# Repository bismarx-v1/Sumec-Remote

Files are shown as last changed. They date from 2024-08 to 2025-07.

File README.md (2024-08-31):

# IR Remote for SUMEC MiniSumo robot

## Description
Sumec-Remote repo contains files that are forked from p1rse as well as our own software, hardware and documentation for IR MiniSumo remote.

## Contents

- **-CODE-** Contains flashed code on the remote.
  
- **-DOCS-** Includes documentation about the project.

- **-PCB-** Includes schematics, bill of materials and pcb files. Schematic and PCBs are created using KiCAD.

## Contact
If you have any questions, suggestions, or issues regarding this project, please feel free to contact us: 

Email - savvapopov1804@gmail.com
LinkedIn - www.linkedin.com/in/popovsavvaprosek/

And follow us on the social media! 
Instagram - @sumec_minisumo_bot

**Sending love, from Czech Republic!**

## For information about the start module and its usage visit: http://www.startmodule.com

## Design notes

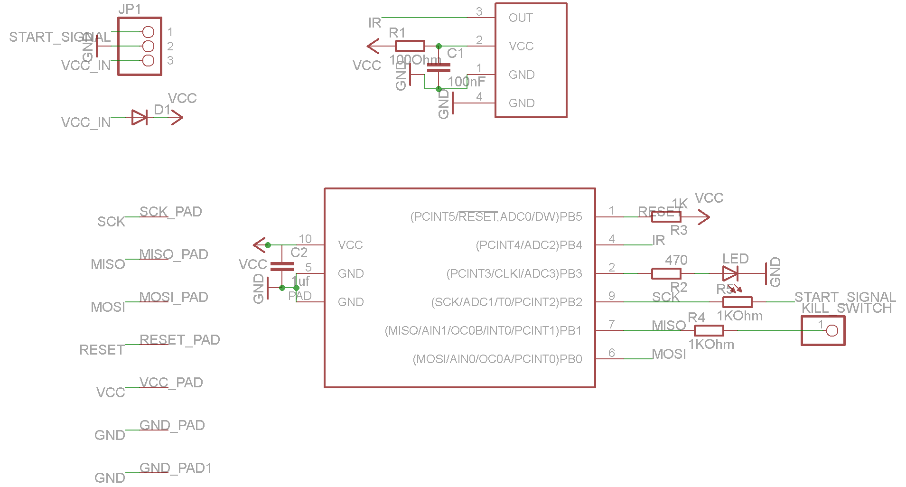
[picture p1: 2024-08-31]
_orig_main/Hardware/Prebuilt_Module/Version_0.16/Schematic_start_module_sumo_IR_V0_16.png

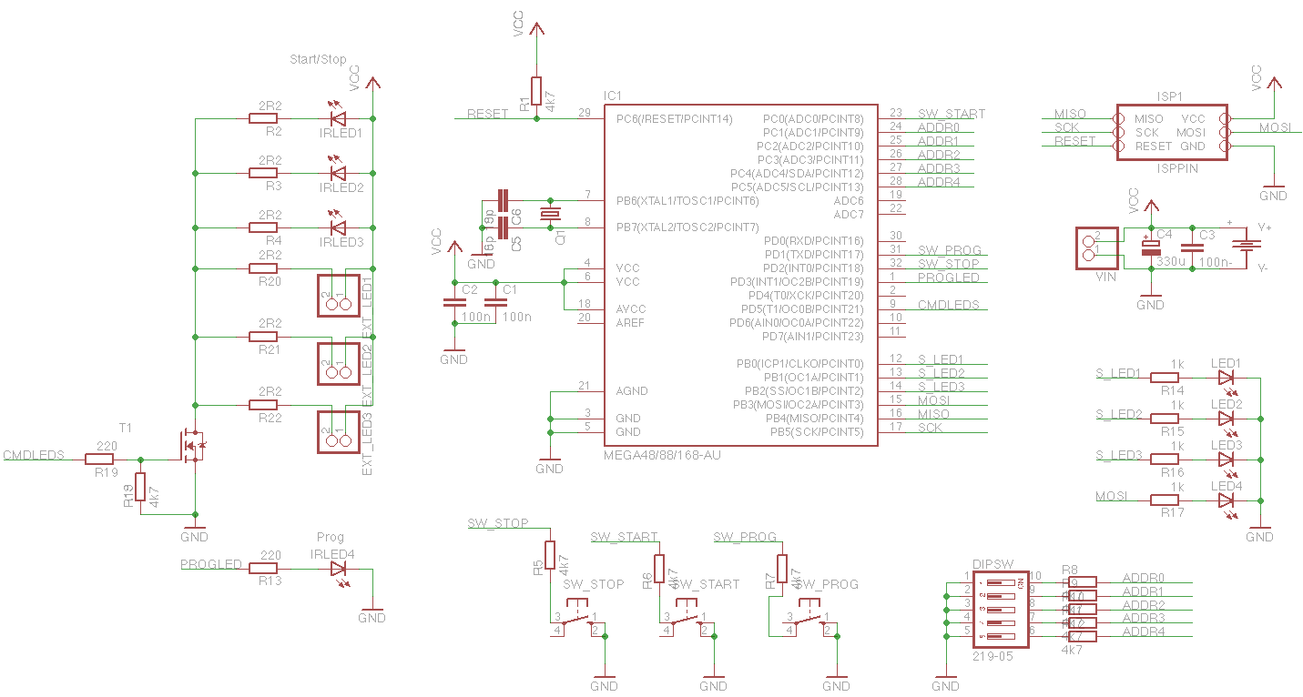
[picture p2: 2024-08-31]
_orig_main/Hardware/Remote_Control/Version_0.04/remote_schematic.png

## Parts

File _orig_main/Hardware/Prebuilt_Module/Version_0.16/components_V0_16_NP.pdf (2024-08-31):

Cost

Component | Package | value | Manufacturer | Mouser (part no) | 100.000 | 500.000 | 1000.000 | function
1 | ATTINY13A-MMU | MLF-10 | 556-ATTINY13A-MMU
IR | 1 | IR-receiver
LED | 1 | Green led | 0603 | 859-LTST-C190GKT | LED indications
C1,C2 | 2 | Capacitance | 0603 | 1uf | 810-C1608X7R1C105M
R1 | 1 | Resistance | 0603 | 100ohm | 667-ERJ-3GEYJ101V | to IR-receiver
R2 | 1 | Resistance | 0603 | 470ohm | 667-ERJ-3GEYJ471V
R3,R4,R5 | 3 | Resistance | 0603 | 1kohm | 667-ERJ-3GEYJ102V | pull up for signals out, pull up reset
D1 | 1 | Schottky Diode | SOD523 | 771-RB751S40,115
| | | | | 0.000 | 0.000 | 0.000
| | | | | 0.000 | 0.000 | 0.000

name in
schematic

amount per
board
uC | Atmel | Microcontroller
TSOP75338WTT 1 | Vishay
| | to Microcontroller and IR-receiver
| | resitor for LED
| | reverse polarity protection, as well as some noise cancelation
total (excl VAT)
total (inkl 20% VAT)

Note 1: Mouser doesn't keep this unit in stock, they do however keep TSOP75338WTR
the only difference is how they are packaged in the tape but for pick and place machines this can cause problems.

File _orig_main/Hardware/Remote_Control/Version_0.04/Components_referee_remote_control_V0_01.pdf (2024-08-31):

Sida

Name | Component | Quantity | Mouser article number | Total Price | Comments
B1 | Battery holder, 2xAA | 1 12BH212P-GR | 1.16 | 1.16
C1-C3 | 100nF | 3 581-08055C104J | 0.041 | 0.123
C4 | Capacitor, C6 (ø6.3mm), 330uF | 1 598-AVE337M06X16T-F | 0.083 | 0.083
C5-C6 | 18pF (optional) | 2 140-CC501N180J-RC | 0.053 | 0.106
Q1 | Crystal (optional), HC49S | 1 815-ABL-16-B2 | 0.27 | 0.27
DIPSW | 1 774-2195MST | 0.66 | 0.66
EXT_LED1-EXT_LED3 | 3 649-68000-420HLF | 0.041 | 0.123 20 pins total
IC1 | 1 556-ATMEGA168PA-AU | 2.1 | 2.1
IRLED1 - IRLED4 | 5mm IR LED | 4 78-TSUS5400 | 0.182 | 0.728
ISP | 1 649-67996-420HLF | 0.048 | 0.048 20 pins total
LED1-LED4 | 4 645-598-8170-107F | 0.1 | 0.4 Average price
T1 | MOSFET, N-channel, sot23, 6.5A | 1 621-DMG6968U-7 | 0.454 | 0.454
R1,R5-R12, R18 | 4k7 | 10 667-ERJ-6GEYJ472V | 0.033 | 0.33
R2-R4, R20-R22 | 2R2 | 6 667-ERJ-6GEYJ2R2V | 0.033 | 0.198
R13, R19 | 220 | 2 667-ERJ-6GEYJ221V | 0.033 | 0.066
R14-R17 | 1k | 4 667-ERJ-6GEYJ102V | 0.033 | 0.132
SW_PROG, SW_START, SW_STOP | Tactile switch, SKHHBV, pin, 6x6mm | 3 688-SKHHBV | 0.215 | 0.645
PCB | 1 N/A | 3 | 3 @10pcs
10.626 <-Total

Price (1pcs, €, excl. vat)

Dipswitch, 5 pol
Pinheader, 1x2
Atmega48/88/168-AU

Pinheader, 2x3
Indication LED, 0805, any colour, Vf<3V SOT223 – 771-BUK9880-55135

By sternå

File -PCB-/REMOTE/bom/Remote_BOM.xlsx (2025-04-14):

Value | Link | Reserve | Quantity | Footprint
10uF | 10uF, 16V, 1206, tantal, mouser (https://cz.mouser.com/ProductDetail/KEMET/T491A106K016AT) | >30 | 2 | CP_EIA-3216-18_Kemet-A_Pad1.58x1.35mm_HandSolder
100nF | 100nF, 16V, 0805, ceramic, mouser X7R (https://cz.mouser.com/ProductDetail/YAGEO/AC0805KRX7R7BB104) | >80 | 2 | C_0805_2012Metric_Pad1.18x1.45mm_HandSolder
18pF | 18pF, 16V, 0805, ceramic, mouser (https://cz.mouser.com/ProductDetail/KYOCERA-AVX/0805YA180JAT2A?qs=nl0EtZFOfLiGc7H%252BYUnNHw%3D%3D) |  | 2 | C_0805_2012Metric_Pad1.18x1.45mm_HandSolder
10k | 10k, 250mW, 0805, mouser (https://cz.mouser.com/ProductDetail/Vishay-Dale/RCC080510K0FKEA?qs=GedFDFLaBXGY93oge9hajw%3D%3D) |  | 5 | R_0805_2012Metric_Pad1.20x1.40mm_HandSolder
1k | 1k. 500mW, 0805, mouser (https://cz.mouser.com/ProductDetail/Vishay-Dale/CRCW08051K00FKEAHP?qs=FlFvgi4rxBy%252Bn2DMV%2FkIbA%3D%3D) |  | 4 | R_0805_2012Metric_Pad1.20x1.40mm_HandSolder
200R | 200R, 500mW, 0805, mouser (https://cz.mouser.com/ProductDetail/Vishay-Dale/CRCW0805200RFKEAHP?qs=2Xec%252BEQj5n%252BcRsKDNXpbZw%3D%3D) |  | 2 | R_0805_2012Metric_Pad1.20x1.40mm_HandSolder
2.2R | 2.2R, 500mW, 0805, mouser (https://cz.mouser.com/ProductDetail/Vishay-Dale/CRCW08052R20FKEAHP?qs=40TFAHZMFvc8altFjF5kRw%3D%3D) |  | 3 | R_0805_2012Metric_Pad1.20x1.40mm_HandSolder
YC248-JR-0710KL | 10k, 8x0402, mouser (https://cz.mouser.com/ProductDetail/YAGEO/YC248-JR-0710KL?qs=8cPjvKtxWv7XgZyJevtvWg%3D%3D) |  | 1 | resistor_array
LED | Yellow, Red, Green (NIO) | 8,8,18 | 4 | LED_0805_2012Metric_Pad1.15x1.40mm_HandSolder
IR204A | IR LED, 50mA, 1.3V, mouser (https://cz.mouser.com/ProductDetail/ROHM-Semiconductor/SIR-34ST3F?qs=4kLU8WoGk0sGjEX1Vu2vfA%3D%3D) |  | 4 | LED_D3.0mm_Horizontal_O3.81mm_Z10.0mm | Red LED, 20mA 1.9V, 0805, mouser (https://cz.mouser.com/ProductDetail/Stanley-Electric/VFHV1112H-3BZ2B-TR?qs=byeeYqUIh0PKiA%252BYRcKo5Q%3D%3D)
Crystal - ABM8G | 16 MHz, 18 pF, mouser (https://www.mouser.co.uk/ProductDetail/ABRACON/ABM8G-16.000MHZ-18-D2Y-T?qs=3LVMET7lfiPkoUdIbdKAPg%3D%3D) |  | 1 | crystal_smd | Yellow LED, 20mA, 1.9V, 0805, mouser (https://cz.mouser.com/ProductDetail/Stanley-Electric/FY1112H-TR?qs=byeeYqUIh0M%2F1I90%252BhjkXg%3D%3D)
DMG6968U-7 | NMOS, SOT23-3, mouser (https://eu.mouser.com/ProductDetail/Diodes-Incorporated/DMG6968U-7?qs=oUsD4qhOtFxfxyoeWY4RMA%3D%3D) |  | 1 | TSOT-23-3_HandSoldering | Green-Yellow LED, 20mA, 1.9V, mouser (https://cz.mouser.com/ProductDetail/Stanley-Electric/VFHD1112H-3B72B-TR?qs=byeeYqUIh0N1xLw8fV03PA%3D%3D)
ATmega168PA-AU | TQFP-32, 1.8 - 5.5 [V], mouser (https://cz.mouser.com/ProductDetail/Microchip-Technology/ATMEGA168PA-AU?qs=rBGENRD8NwK93x8%252BpfprPQ%3D%3D) |  | 1 | TQFP-32_7x7mm_P0.8mm
SW_Push | Height 8mm, Width 6mm, mouser (https://cz.mouser.com/ProductDetail/TE-Connectivity-AMP/FSM11JLH?qs=P19jvy6W2mdQ1kTiQwvziQ%3D%3D) |  | 3 | SW_PUSH_6mm
DS04-254-1-05BK-SMT | 5P, 2.54mm, DIP, mouser (https://cz.mouser.com/ProductDetail/CUI-Devices/DS04-254-1-05BK-SMT?qs=wnTfsH77Xs5Ndj%252Bt08dChA%3D%3D) |  | 1 | dip_switch
Battery | Keystone_2462, 2xAA, mouser (https://cz.mouser.com/ProductDetail/Keystone-Electronics/2462?qs=3CbvriavsLChvFNADwDLZA%3D%3D) |  | 1 | BatteryHolder_Keystone_2462_2xAA - no holes
AVR-ISP-6 | GME |  | 1 | PinHeader_2x03_P2.54mm_Vertical
NIO - Not in order

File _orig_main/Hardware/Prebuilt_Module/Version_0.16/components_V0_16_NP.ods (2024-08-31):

 |  |  |  |  |  |  |  | Cost
name in schematic | amount per board | Component | Package | value | Manufacturer | Mouser (part no) | 100.000 | 500.000 | 1000.000 | function
uC | 1 | ATTINY13A-MMU | MLF-10 |  | Atmel | 556-ATTINY13A-MMU |  |  |  | Microcontroller
IR | 1 | TSOP75338WTT 1 |  |  | Vishay |  |  |  |  | IR-receiver
LED | 1 | Green led | 0603 |  |  | 859-LTST-C190GKT |  |  |  | LED indications
C1,C2 | 2 | Capacitance | 0603 | 1uf |  | 810-C1608X7R1C105M |  |  |  | to Microcontroller and IR-receiver
R1 | 1 | Resistance | 0603 | 100ohm |  | 667-ERJ-3GEYJ101V |  |  |  | to IR-receiver
R2 | 1 | Resistance | 0603 | 470ohm |  | 667-ERJ-3GEYJ471V |  |  |  | resitor for LED
R3,R4,R5 | 3 | Resistance | 0603 | 1kohm |  | 667-ERJ-3GEYJ102V |  |  |  | pull up for signals out, pull up reset
D1 | 1 | Schottky Diode | SOD523 |  |  | 771-RB751S40,115 |  |  |  | reverse polarity protection, as well as some noise cancelation
 |  | total (excl VAT) |  |  |  |  | 0.000 | 0.000 | 0.000
 |  | total (inkl 20% VAT) |  |  |  |  | 0.000 | 0.000 | 0.000
 |  | Note 1: Mouser doesn't keep this unit in stock, they do however keep TSOP75338WTR the only difference is how they are packaged in the tape but for pick and place machines this can cause problems.

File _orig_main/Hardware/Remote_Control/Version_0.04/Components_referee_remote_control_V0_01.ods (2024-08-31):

Name | Component | Quantity | Mouser article number | Price (1pcs, €, excl. vat) | Total Price | Comments
B1 | Battery holder, 2xAA | 1 | 12BH212P-GR | 1.16 | 1.16
C1-C3 | 100nF | 3 | 581-08055C104J | 0.041 | 0.123
C4 | Capacitor, C6 (ø6.3mm), 330uF | 1 | 598-AVE337M06X16T-F | 0.083 | 0.083
C5-C6 | 18pF (optional) | 2 | 140-CC501N180J-RC | 0.053 | 0.106
Q1 | Crystal (optional), HC49S | 1 | 815-ABL-16-B2 | 0.27 | 0.27
DIPSW | Dipswitch, 5 pol | 1 | 774-2195MST | 0.66 | 0.66
EXT_LED1-EXT_LED3 | Pinheader, 1x2 | 3 | 649-68000-420HLF | 0.041 | 0.123 | 20 pins total
IC1 | Atmega48/88/168-AU | 1 | 556-ATMEGA168PA-AU | 2.1 | 2.1
IRLED1 - IRLED4 | 5mm IR LED | 4 | 78-TSUS5400 | 0.182 | 0.728
ISP | Pinheader, 2x3 | 1 | 649-67996-420HLF | 0.048 | 0.048 | 20 pins total
LED1-LED4 | Indication LED, 0805, any colour, Vf<3V | 4 | 645-598-8170-107F | 0.1 | 0.4 | Average price
T1 | MOSFET, N-channel, sot23, 6.5A | 1 | 621-DMG6968U-7 | 0.454 | 0.454 | SOT223 – 771-BUK9880-55135
R1,R5-R12, R18 | 4k7 | 10 | 667-ERJ-6GEYJ472V | 0.033 | 0.33
R2-R4, R20-R22 | 2R2 | 6 | 667-ERJ-6GEYJ2R2V | 0.033 | 0.198
R13, R19 | 220 | 2 | 667-ERJ-6GEYJ221V | 0.033 | 0.066
R14-R17 | 1k | 4 | 667-ERJ-6GEYJ102V | 0.033 | 0.132
SW_PROG, SW_START, SW_STOP | Tactile switch, SKHHBV, pin, 6x6mm | 3 | 688-SKHHBV | 0.215 | 0.645
PCB | By sternå | 1 | N/A | 3 | 3 | @10pcs
 |  |  |  |  | 10.626 | <-Total

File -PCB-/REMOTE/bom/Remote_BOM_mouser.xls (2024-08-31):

Mfr Part Number (Input) | Manufacturer Part Number | Mouser Part Number | Manufacturer Name | Description | Quantity 1 | Unit Price 1 | Quantity 2 | Unit Price 2 | Quantity 3 | Unit Price 3 | Quantity 4 | Unit Price 4 | Quantity 5 | Unit Price 5 | Order Quantity | Order Unit Price | Min./Mult. | Availability | Lead Time in Days | Lifecycle | NCNR | RoHS | Pb Free | Package Type | Datasheet URL | Product Image | Design Risk
 |  | 581-0805YA180JAT2A |  |  | 10
 |  | 71-RCC080510K0FKEA |  |  | 100
 |  | 71-CRCW08051K00FKEAH |  |  | 10
 |  | 71-CRCW0805200RFKEAH |  |  | 10
 |  | 71-CRCW08052R20FKEAH |  |  | 10
 |  | 603-YC248-JR-0710KL |  |  | 10
 |  | 755-SIR-34ST3F |  |  | 10
 |  | 815-ABM8G-16-18D2Y |  |  | 10
 |  | 621-DMG6968U-7 |  |  | 10
 |  | 556-ATMEGA168PA-AU |  |  | 3
 |  | 506-FSM11JLH |  |  | 10
 |  | 490-DS04254105BK-SMT |  |  | 3
 |  | 534-2462 |  |  | 3

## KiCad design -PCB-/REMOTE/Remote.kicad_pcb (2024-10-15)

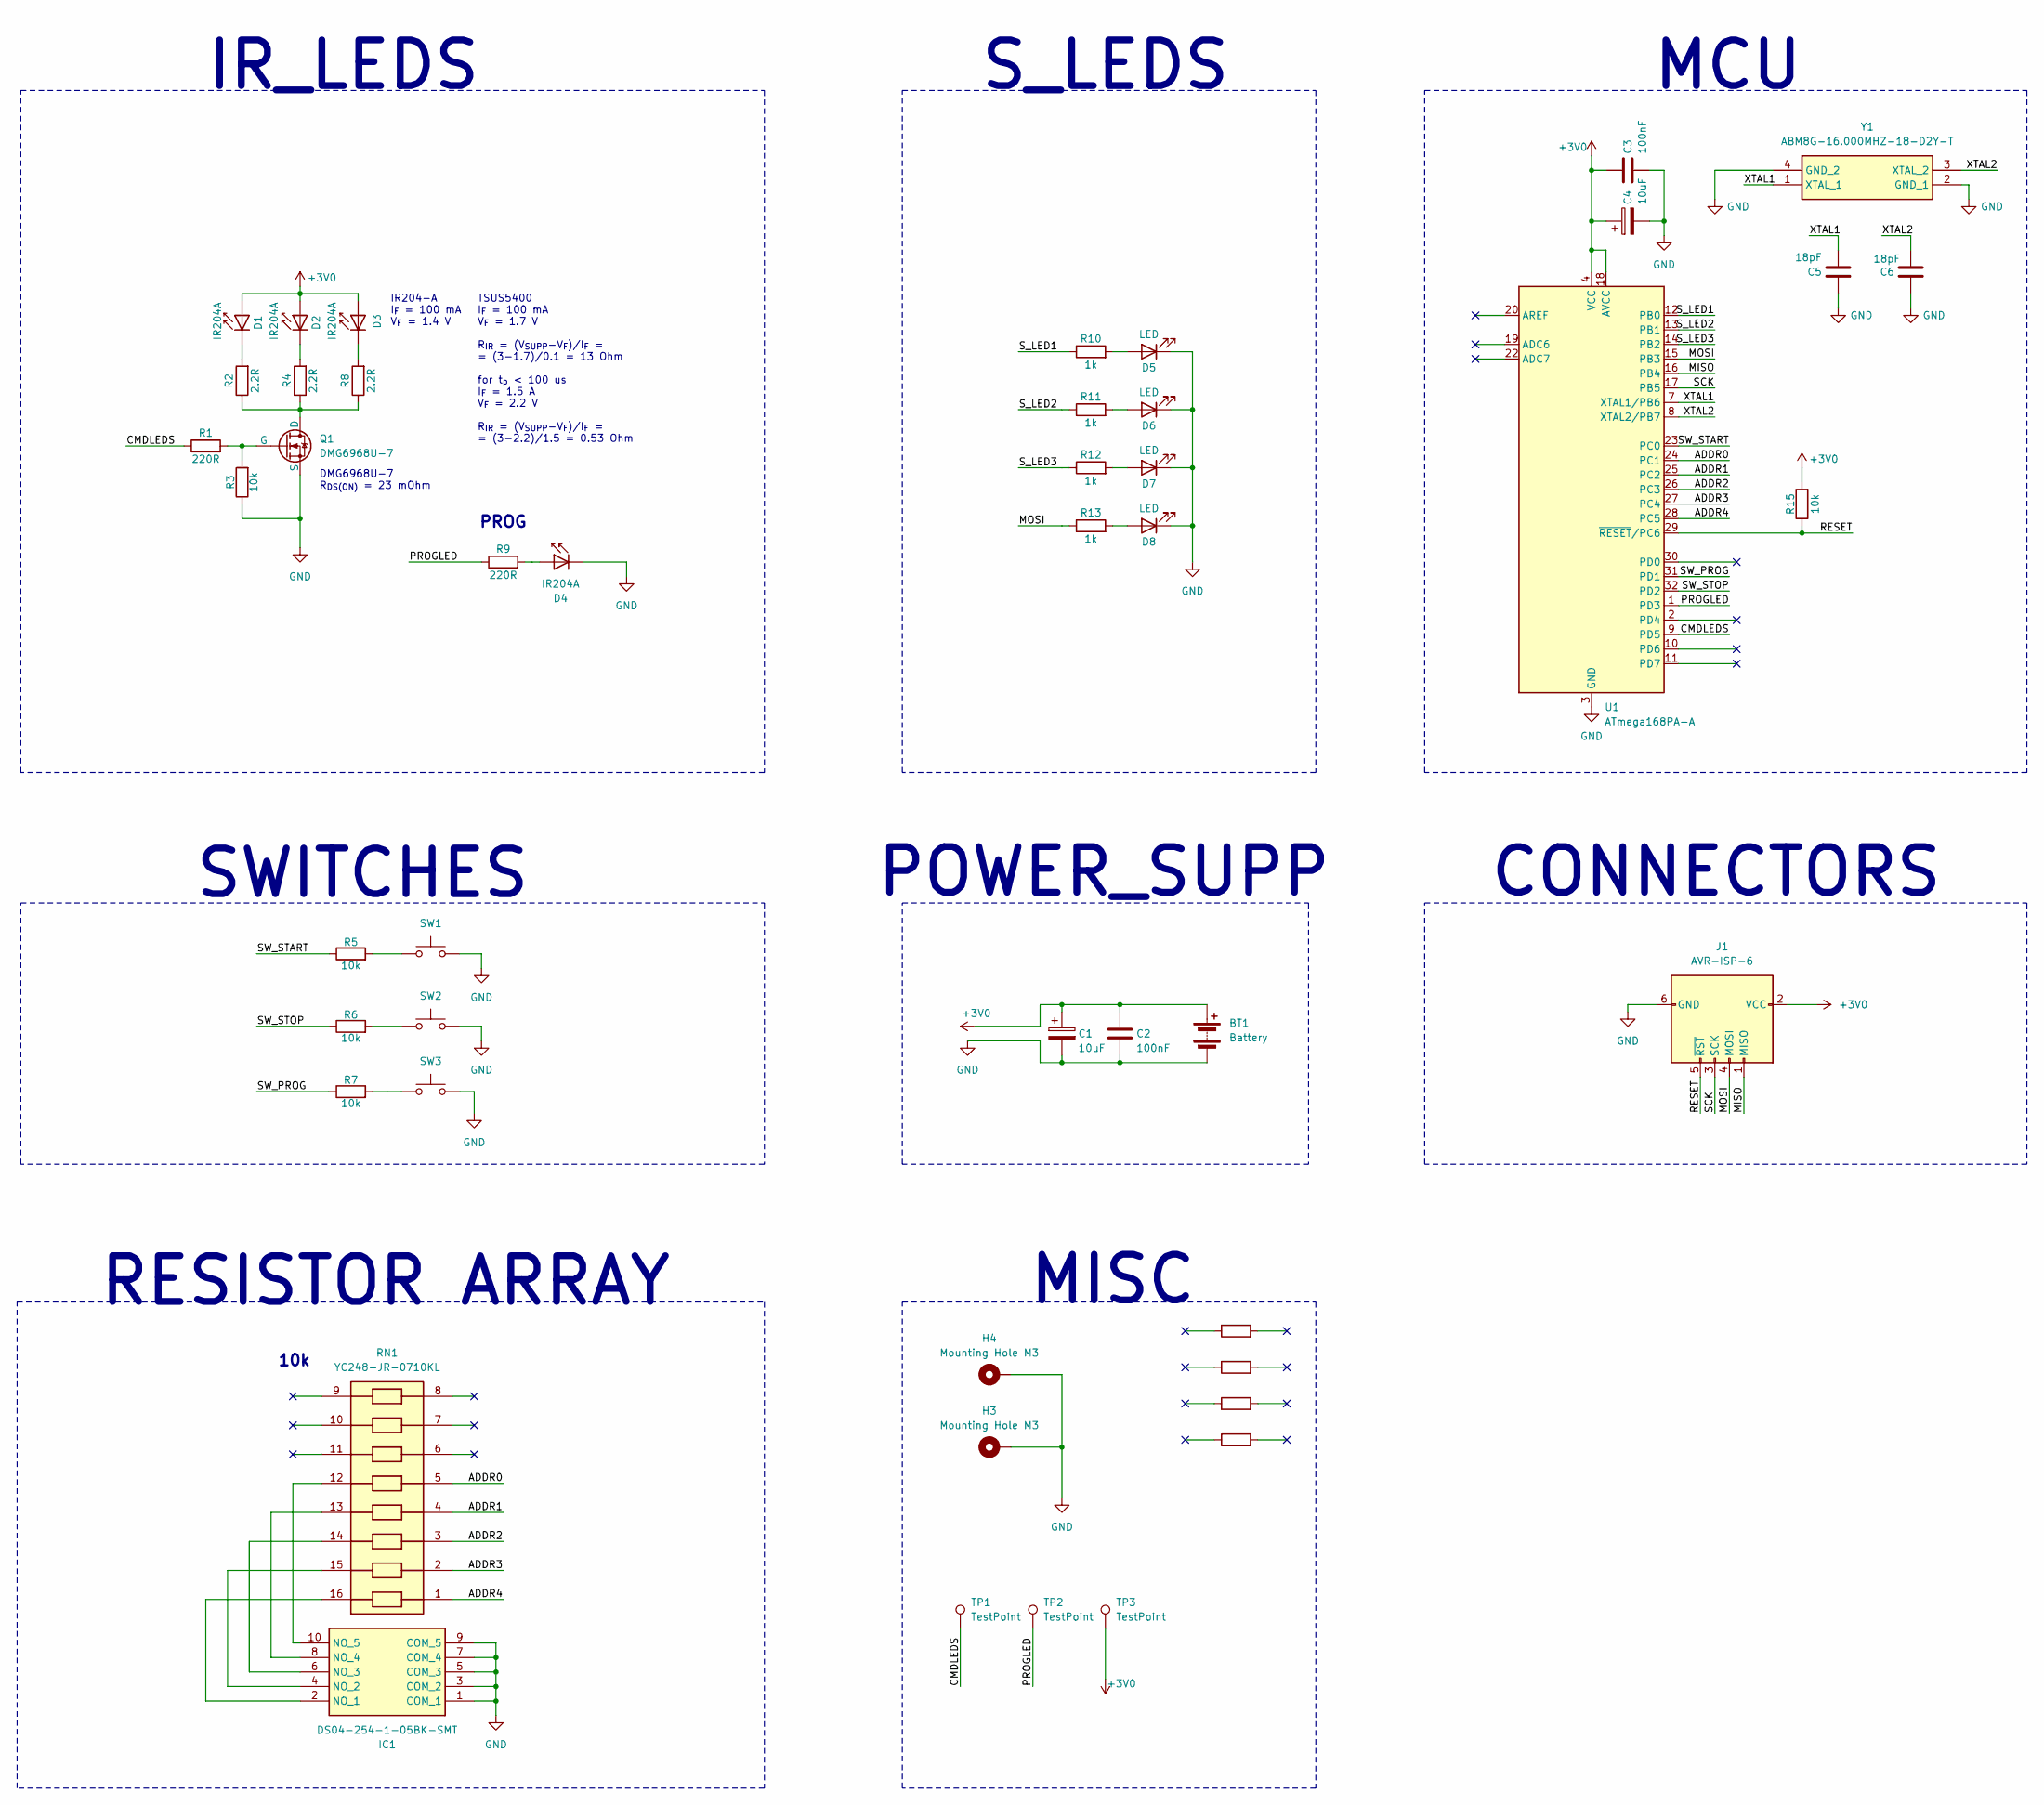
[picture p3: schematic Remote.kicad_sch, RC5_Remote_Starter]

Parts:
BT1: Battery; BatteryHolder_Keystone_2462_2xAA - no holes
C1, C4: 10uF; CP_EIA-3216-18_Kemet-A_Pad1.58x1.35mm_HandSolder
C2, C3: 100nF; C_0805_2012Metric_Pad1.18x1.45mm_HandSolder
C5, C6: 18pF; C_0805_2012Metric_Pad1.18x1.45mm_HandSolder
D1, D3: IR204A; LED_D3.0mm_Horizontal_O3.81mm_Z10.0mm_no_silk
D2: IR204A; LED_D3.0mm_Horizontal_O3.81mm_Z10.0mm_flipped_no_silk
D4: IR204A; LED_D3.0mm_Horizontal_O3.81mm_Z10.0mm_flipped
D5, D6, D7, D8: LED; LED_0805_2012Metric_Pad1.15x1.40mm_HandSolder
H3, H4: Mounting Hole M3; MountingHole_3.2mm_M3_Pad_Via
IC1: DS04-254-1-05BK-SMT; dip_switch; Mouser Part Number 490-DS04254105BK-SMT
J1: AVR-ISP-6; PinHeader_2x03_P2.54mm_Vertical
Q1: DMG6968U-7; SOT-23-3
R1, R9: 220R; R_0805_2012Metric_Pad1.20x1.40mm_HandSolder
R2, R4, R8: 2.2R; R_0805_2012Metric_Pad1.20x1.40mm_HandSolder
R3, R5, R6, R7, R15: 10k; R_0805_2012Metric_Pad1.20x1.40mm_HandSolder
R10, R11, R12, R13: 1k; R_0805_2012Metric_Pad1.20x1.40mm_HandSolder
R14: R; purosidenegative
R16: R; SPS LOGO
R17: R; boi
R18: R; Logo
RN1: YC248-JR-0710KL; resistor_array; Mouser Part Number 603-YC248-JR-0710KL
SW1, SW2, SW3: SW_Push; SW_PUSH_6mm
TP1, TP2, TP3: TestPoint; TestPoint_Pad_D1.5mm
U1: ATmega168PA-A; TQFP-32_7x7mm_P0.8mm
Y1: ABM8G-16.000MHZ-18-D2Y-T; crystal_smd; Mouser Part Number 815-ABM8G-16-18D2Y

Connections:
+3V0: BT1.1 (+), C1.1, C2.1, C3.1, C4.1, D1.2 (A), D2.2 (A), D3.2 (A), J1.2 (VCC), R15.2, TP3.1, U1.4 (VCC), U1.6 (VCC), U1.18 (AVCC)
/ADDR0: RN1.5, U1.24 (PC1)
/ADDR1: RN1.4, U1.25 (PC2)
/ADDR2: RN1.3, U1.26 (PC3)
/ADDR3: RN1.2, U1.27 (PC4)
/ADDR4: RN1.1, U1.28 (PC5)
/CMDLEDS: R1.1, TP1.1, U1.9 (PD5)
/MISO: J1.1 (MISO), U1.16 (PB4)
/MOSI: J1.4 (MOSI), R13.1, U1.15 (PB3)
/PROGLED: R9.1, TP2.1, U1.1 (PD3)
/RESET: J1.5 (~RST), R15.1, U1.29 (~RESET/PC6)
/SCK: J1.3 (SCK), U1.17 (PB5)
/SW_PROG: R7.1, U1.31 (PD1)
/SW_START: R5.1, U1.23 (PC0)
/SW_STOP: R6.1, U1.32 (PD2)
/S_LED1: R10.1, U1.12 (PB0)
/S_LED2: R11.1, U1.13 (PB1)
/S_LED3: R12.1, U1.14 (PB2)
/XTAL1: C5.2, U1.7 (XTAL1/PB6), Y1.1 (XTAL_1)
/XTAL2: C6.2, U1.8 (XTAL2/PB7), Y1.3 (XTAL_2)
GND: BT1.2 (-), C1.2, C2.2, C3.2, C4.2, C5.1, C6.1, D4.1 (K), D5.1 (K), D6.1 (K), D7.1 (K), D8.1 (K), H3.1, H4.1, IC1.1 (COM_1), IC1.3 (COM_2), IC1.5 (COM_3), IC1.7 (COM_4), IC1.9 (COM_5), J1.6 (GND), Q1.3 (S), R3.1, SW1.2, SW2.2, SW3.2, U1.3 (GND), U1.5 (GND), U1.21 (GND), Y1.2 (GND_1), Y1.4 (GND_2)
unnamed: D1.1 (K), R2.2
unnamed: D2.1 (K), R4.2
unnamed: D3.1 (K), R8.2
unnamed: D4.2 (A), R9.2
unnamed: D5.2 (A), R10.2
unnamed: D6.2 (A), R11.2
unnamed: D7.2 (A), R12.2
unnamed: D8.2 (A), R13.2
unnamed: IC1.2 (NO_1), RN1.16
unnamed: IC1.4 (NO_2), RN1.15
unnamed: IC1.6 (NO_3), RN1.14
unnamed: IC1.8 (NO_4), RN1.13
unnamed: IC1.10 (NO_5), RN1.12
unnamed: Q1.1 (D), R2.1, R4.1, R8.1
unnamed: Q1.2 (G), R1.2, R3.2
unnamed: R5.2, SW1.1
unnamed: R6.2, SW2.1
unnamed: R7.2, SW3.1

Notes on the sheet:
MISC
MCU
IR204-A I_{F} = 100 mA V_{F} = 1.4 V
SWITCHES
10k
POWER_SUPP
RESISTOR ARRAY
TSUS5400 I_{F} = 100 mA V_{F} = 1.7 V R_{IR} = (V_{SUPP}-V_{F})/I_{F} = = (3-1.7)/0.1 = 13 Ohm for t_{p} < 100 us I_{F} = 1.5 A V_{F} = 2.2 V R_{IR} = (V_{SUPP}-V_{F})/I_{F} = = (3-2.2)/1.5 = 0.53 Ohm
S_LEDS
CONNECTORS
IR_LEDS
PROG
DMG6968U-7 R_{DS(ON)} = 23 mOhm

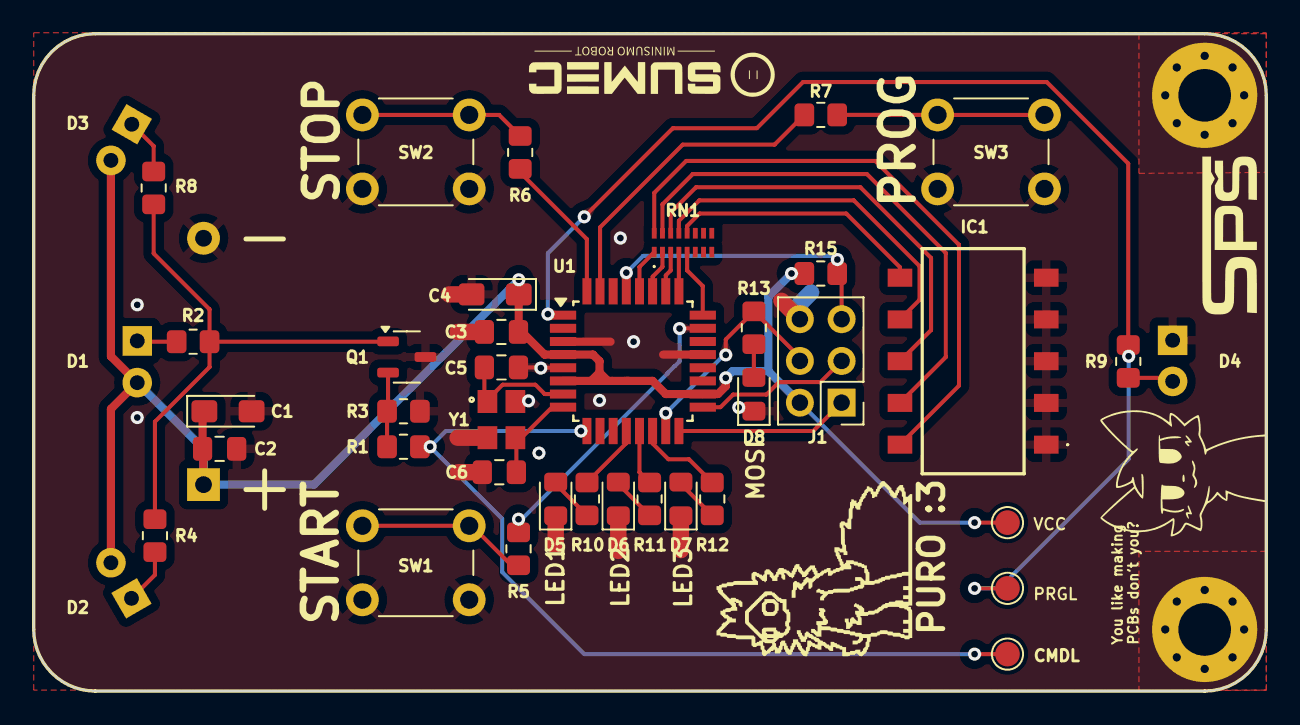
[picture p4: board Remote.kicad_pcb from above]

Board: 2 copper layers, 75.0 x 40.0 mm, 47 parts (1 on the bottom side), 39 nets.

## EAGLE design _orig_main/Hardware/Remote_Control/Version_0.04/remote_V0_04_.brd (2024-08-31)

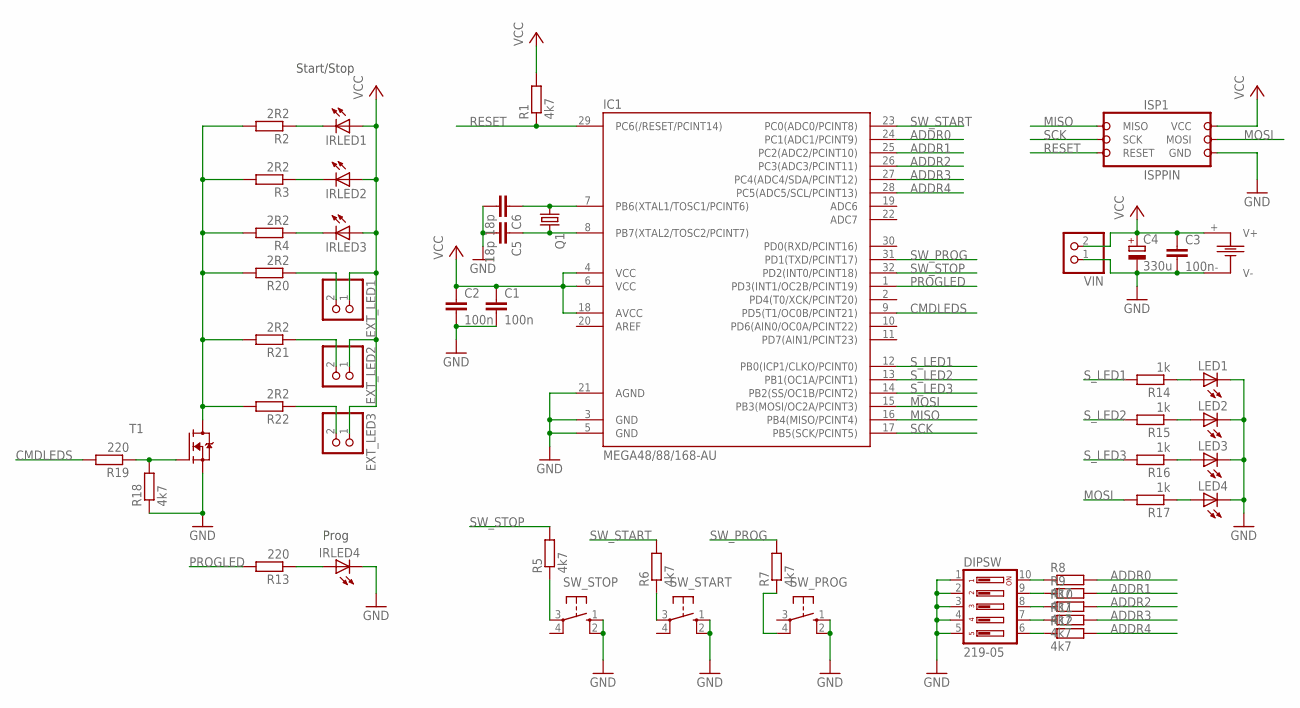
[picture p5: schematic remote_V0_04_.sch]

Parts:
B1: BATTERY_HOLDER_1; BAT_HOLDER_1
C1, C2, C3: 100n; C0805WP
C4: 330u; SANYO-OSCON_SMD_C6
C5, C6: 18p; C0805WP
DIPSW: 219-05; CTS-219-05
EXT_LED1, EXT_LED2, EXT_LED3: PINHD-1X2LONG; 1X2LONG
IC1: MEGA48/88/168-AU; TQFP32-08
IRLED1, IRLED2, IRLED3, IRLED4: LEDLED5MMH; LED5MMH
ISP1: ISPPIN; 2X03
LED1, LED2, LED3, LED4: LED0805; LED_0805
Q1: CRYSTALHC49S; HC49/S
R1, R5, R6, R7, R8, R9, R10, R11, R12, R18: 4k7; R0805WP
R2, R3, R4, R20, R21, R22: 2R2; R0805WP
R13, R19: 220; R0805WP
R14, R15, R16, R17: 1k; R0805WP
SW_PROG: 10-XX; B3F-10XX
SW_START: 10-XX; B3F-10XX
SW_STOP: 10-XX; B3F-10XX
T1: MOSFET_N_SOT23; SOT23
VIN: PINHD-1X2; 1X02

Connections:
ADDR0: IC1.24 (PC1(ADC1/PCINT9)), R8.2
ADDR1: IC1.25 (PC2(ADC2/PCINT10)), R9.2
ADDR2: IC1.26 (PC3(ADC3/PCINT11)), R10.2
ADDR3: IC1.27 (PC4(ADC4/SDA/PCINT12)), R11.2
ADDR4: IC1.28 (PC5(ADC5/SCL/PCINT13)), R12.2
CMDLEDS: IC1.9 (PD5(T1/OC0B/PCINT21)), R19.2
GND: B1.- (V-), C1.2, C2.2, C3.2, C4.-, C5.2, C6.2, DIPSW.1, DIPSW.2, DIPSW.3, DIPSW.4, DIPSW.5, IC1.3 (GND), IC1.5 (GND), IC1.21 (AGND), IRLED4.P$2 (C), ISP1.6 (GND), LED1.C, LED2.C, LED3.C, LED4.C, R18.1, SW_PROG.1 (S), SW_PROG.2 (S1), SW_START.1 (S), SW_START.2 (S1), SW_STOP.1 (S), SW_STOP.2 (S1), T1.2 (S), VIN.1
MISO: IC1.16 (PB4(MISO/PCINT4)), ISP1.1 (MISO)
MOSI: IC1.15 (PB3(MOSI/OC2A/PCINT3)), ISP1.4 (MOSI), R17.2
unnamed: IRLED1.P$2 (C), R2.1
unnamed: IRLED2.P$2 (C), R3.1
unnamed: IRLED3.P$2 (C), R4.1
unnamed: DIPSW.10, R8.1
unnamed: DIPSW.9, R9.1
unnamed: DIPSW.8, R10.1
unnamed: DIPSW.7, R11.1
unnamed: DIPSW.6, R12.1
unnamed: R5.1, SW_STOP.3
unnamed: R6.1, SW_START.3
unnamed: R7.1, SW_PROG.4 (P1)
unnamed: IRLED4.P$1 (A), R13.1
unnamed: R18.2, R19.1, T1.1 (G)
unnamed: LED1.A, R14.1
unnamed: LED2.A, R15.1
unnamed: LED3.A, R16.1
unnamed: LED4.A, R17.1
unnamed: C6.1, IC1.7 (PB6(XTAL1/TOSC1/PCINT6)), Q1.1
unnamed: EXT_LED1.2, R20.1
unnamed: EXT_LED2.2, R21.1
unnamed: R2.2, R3.2, R4.2, R20.2, R21.2, R22.2, T1.3 (D)
unnamed: EXT_LED3.2, R22.1
unnamed: C5.1, IC1.8 (PB7(XTAL2/TOSC2/PCINT7)), Q1.2
PROGLED: IC1.1 (PD3(INT1/OC2B/PCINT19)), R13.2
RESET: IC1.29 (PC6(/RESET/PCINT14)), ISP1.5 (RESET), R1.1
SCK: IC1.17 (PB5(SCK/PCINT5)), ISP1.3 (SCK)
SW_PROG: IC1.31 (PD1(TXD/PCINT17)), R7.2
SW_START: IC1.23 (PC0(ADC0/PCINT8)), R6.2
SW_STOP: IC1.32 (PD2(INT0/PCINT18)), R5.2
S_LED1: IC1.12 (PB0(ICP1/CLKO/PCINT0)), R14.2
S_LED2: IC1.13 (PB1(OC1A/PCINT1)), R15.2
S_LED3: IC1.14 (PB2(SS/OC1B/PCINT2)), R16.2
VCC: B1.+ (V+), C1.1, C2.1, C3.1, C4.+, EXT_LED1.1, EXT_LED2.1, EXT_LED3.1, IC1.4 (VCC), IC1.6 (VCC), IC1.18 (AVCC), IRLED1.P$1 (A), IRLED2.P$1 (A), IRLED3.P$1 (A), ISP1.2 (VCC), R1.2, VIN.2

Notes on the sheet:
Start/Stop
Prog

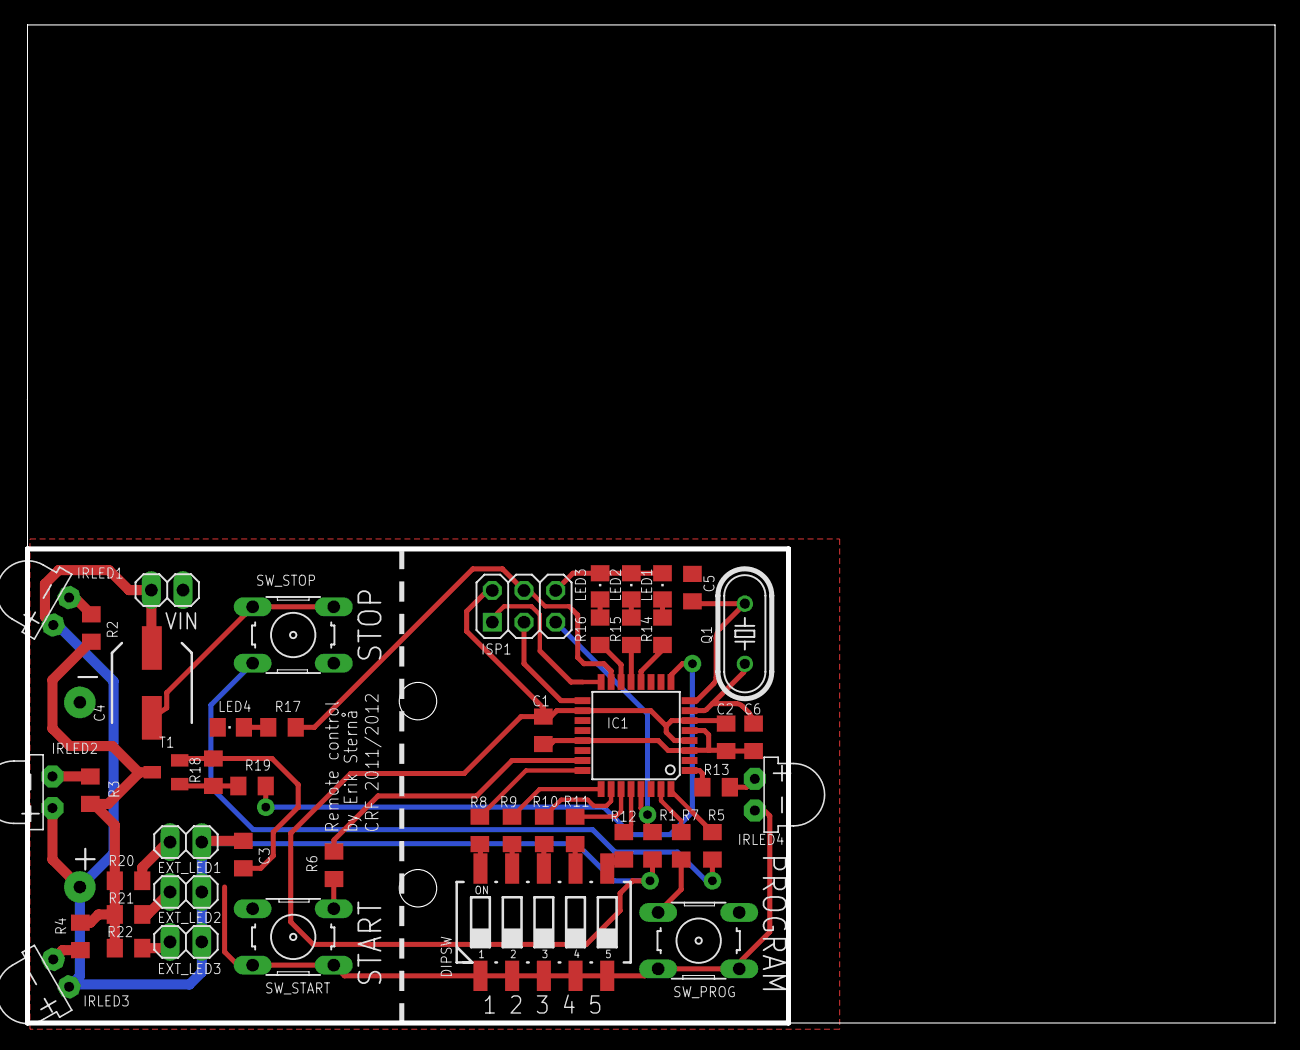
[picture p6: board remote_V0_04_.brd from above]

Board: 2 copper layers, 100.0 x 80.0 mm, 49 parts (1 on the bottom side), 42 nets.

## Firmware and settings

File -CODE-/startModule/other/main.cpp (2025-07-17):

#if 0
/**
 * https://www.instructables.com/ATTiny-Port-Manipulation/
 * https://www.instructables.com/ATtiny85-Interrupt-Barebones-Example/
 * https://en.wikipedia.org/wiki/RC-5
 */

/**
 * This feels like a lot of janky hacked together trash.
 * Hope it works.
 */

  #include <Arduino.h>


  #define PIN_STATE_OUT 3
  #define PIN_IR_INPUT  4
  #define PIN_LED1      1
  #define PIN_LED2      0

  #define RECIEVE_TIMEOUT 3    // In ms. How long since the last trigger should be considered an end.
  #define BIT_MIN_TIME    750  // In us. Anything shorter than this is noise.
  #define BUFFER_SIZE     32


  #define PROTOCOL_RC5    1
  #define RC5_SINGLE_LOW  800
  #define RC5_SINGLE_HIGH 1000
  #define RC5_DOUBLE_LOW  1600
  #define RC5_DOUBLE_HIGH 2000


  #define SET_TO_BIT(BIT, OUT_ARRAY_INDEX, OUT_ARRAY)                                                                          \
    if((BIT) == 0) {                                                                                                           \
      OUT_ARRAY &= 1 << OUT_ARRAY_INDEX;                                                                                       \
    } else {                                                                                                                   \
      OUT_ARRAY |= 0 << OUT_ARRAY_INDEX;                                                                                       \
    }

  #define DIV_TWO_CEIL(SRC, DST)                                                                                               \
    if((SRC & 1) == 1) {                                                                                                       \
      DST = SRC >> 1;                                                                                                          \
      DST = SRC + 1;                                                                                                           \
    } else {                                                                                                                   \
      DST = SRC >> 1;                                                                                                          \
    }



uint64_t             rawBuffer                    = 0;
static const uint8_t rawBufferSize                = (BUFFER_SIZE < sizeof(rawBuffer) * 8 ? BUFFER_SIZE : sizeof(rawBuffer) * 8);
uint16_t             rawBufferTime[rawBufferSize] = {0};
uint8_t              rawBufferIndex               = 0;
uint32_t             recieveTimeoutTime           = -1;



void irInterrupt() {
  static uint32_t timeSinceLastTrig = 0;

  // Read the volatile stuff.
  uint32_t timeNow = micros();
  bool     irVal   = (DDRB >> PIN_IR_INPUT) & PB1;


  // Write the length of the previous bit.
  rawBufferTime[rawBufferIndex] = timeNow - timeSinceLastTrig;

  // Move to the current bit.
  rawBufferIndex++;
  // If buffer full, return.
  if(rawBufferIndex + 1 >= rawBufferSize) {
    return;
  }

  // Add the value to the buffer.
  SET_TO_BIT(irVal, rawBufferIndex, rawBuffer)
  // Update time since last trig.
  timeSinceLastTrig = timeNow;

  // Update the timeout time.
  recieveTimeoutTime = millis() + RECIEVE_TIMEOUT;
}


uint64_t             cleanBuffer     = 0;
static const uint8_t cleanBufferSize = (BUFFER_SIZE < sizeof(cleanBuffer) * 8 ? BUFFER_SIZE : sizeof(cleanBuffer) * 8);
uint16_t             cleanBufferTime[cleanBufferSize] = {0};
uint8_t              cleanBufferIndex                 = 0;

void reduceBuffer() {
  static uint8_t bitWriteIdx = 0;
  for(uint8_t idx = 0; idx < cleanBufferIndex; idx++) {
    static uint8_t bitPrevoius = 0xff;
    bool           bitCurrent  = (cleanBuffer >> idx) & 1;
    if(bitPrevoius == bitCurrent) {
      // Add this bit's length to the prevoius one.
      cleanBufferTime[bitWriteIdx - 1] += cleanBufferTime[idx];
    } else {
      // Just move the bit to a new pos.
      SET_TO_BIT(bitCurrent, cleanBuffer, bitWriteIdx)
      cleanBufferTime[bitWriteIdx] = cleanBufferTime[idx];
      bitWriteIdx++;
    }

    bitPrevoius = bitCurrent;
  }
}


void denoiseBuffer() {
  uint16_t accumulatedTime = 0;
  // Check the length of every bit.
  for(uint8_t idx = 0; idx < rawBufferIndex; idx++) {
    accumulatedTime += rawBufferTime[idx];
    // Isn't noise.
    if(rawBufferTime[idx] >= BIT_MIN_TIME) {
      // Shift the bit into the clean buffer.
      SET_TO_BIT((rawBuffer >> idx) & 1, cleanBufferIndex, cleanBuffer)
      // Set the bits length since the prevoius "clean" bit.
      cleanBufferTime[cleanBufferIndex] = accumulatedTime;
      // Shift and reset.
      cleanBufferIndex++;
      accumulatedTime = 0;
    }
  }

  // Remove repeating bits, join their lengths.
  reduceBuffer();

  // Move the end stop by what's been reduced.
  cleanBufferIndex = accumulatedTime;
}


void resetRawBuffer() {
  memset(rawBufferTime, 0, rawBufferSize);
  rawBufferIndex     = 0;
  rawBuffer          = 0;
  recieveTimeoutTime = -1;
}


void resetCleanBuffer() {
  memset(cleanBufferTime, 0, cleanBufferSize);
  cleanBufferIndex = 0;
  cleanBuffer      = 0;
}


/** TODO: fix this */
uint8_t detectProtocol() {
  return PROTOCOL_RC5;
  return 0;
}


bool decodeRc5(uint8_t*       toggle,
               uint8_t*       address,
               uint8_t*       command,
               const uint64_t buffer,
               uint16_t*      bufferTime,
               const uint8_t  bufferSize) {
  /*for(uint8_t idx = 0; idx < bufferSize; idx++) {  // DEBUG
    Serial.printf("%02x\t%u\t%lu\n", idx, (buffer >> idx) & 1, bufferTime[idx]);
  }*/

  uint64_t decodedBits      = 0;
  uint8_t  decodedBitsIndex = 0;  // 26 or 27
  // Filter rc5 specific lengths.
  for(uint8_t idx = 0; idx < bufferSize; idx++) {
    if(bufferTime[idx] > RC5_SINGLE_LOW && bufferTime[idx] < RC5_SINGLE_HIGH) {
      SET_TO_BIT(((buffer >> idx) & 1), decodedBitsIndex, decodedBits)
      decodedBitsIndex++;
    } else if(bufferTime[idx] > RC5_DOUBLE_LOW && bufferTime[idx] < RC5_DOUBLE_HIGH) {
      SET_TO_BIT(((buffer >> idx) & 1), decodedBitsIndex, decodedBits)
      decodedBitsIndex++;
      SET_TO_BIT(((buffer >> idx) & 1), decodedBitsIndex, decodedBits)
      decodedBitsIndex++;
    }
  }
  if(decodedBitsIndex < 26 || decodedBitsIndex > 27) {
    return 0;
  }


  // Remove the half bit.
  decodedBitsIndex = decodedBitsIndex - 1;
  decodedBits      = decodedBits >> 1;

  // Split the buffer into pairs.
  DIV_TWO_CEIL(decodedBitsIndex, decodedBitsIndex)
  // Take the first bit from the pair.
  for(uint8_t idx = 0; idx < decodedBitsIndex; idx++) {
    SET_TO_BIT(((decodedBits >> idx * 2) & 1), idx, decodedBits)
  }

  // Remove the second start bit.
  decodedBits = decodedBits >> 1;

  *toggle  = decodedBits & 1;
  *address = (decodedBits >> 1) & 0b11111;
  *command = (decodedBits >> 6) & 0b111111;
  return 1;
}


bool irCheck(uint8_t* toggle, uint8_t* address, uint8_t* command) {
  uint8_t returnStatus = 0;
  noInterrupts();
  // Check if the reading has finished.
  if(recieveTimeoutTime <= millis()) {
    denoiseBuffer();

    // Add new protocols here.
    switch(detectProtocol()) {
      case PROTOCOL_RC5:
        returnStatus = decodeRc5(toggle, address, command, cleanBuffer, cleanBufferTime, cleanBufferIndex);
        break;

      default:  // Unknown protocol.
        break;
    }
  }

  // Reset buffer and re-enable interrupts.
  resetRawBuffer();
  resetCleanBuffer();
  interrupts();
  return returnStatus;
}


struct led {
private:
  uint8_t  pin          = -1;
  uint16_t durationHigh = 0;
  uint16_t durationLow  = 0;
  uint8_t  repeats      = 0;
  uint32_t timeStart    = 0;
  uint32_t timeEnd      = 0;

public:
  led(uint8_t pin) {
    this->pin = pin;
    pinMode(pin, OUTPUT);
  }

  void set(uint16_t durationHigh, uint16_t durationLow, uint8_t repeats) {
    this->durationHigh = durationHigh;
    this->durationLow  = durationLow;
    this->repeats      = repeats;
    timeStart          = millis();
    timeEnd            = timeStart + ((durationHigh + durationLow) * repeats);
  }

  void loop() {
    uint32_t timeNow = millis();
    if(timeNow > timeEnd) {
      return;
    }

    uint32_t timeRunning = timeNow - timeStart;
    timeRunning          = timeRunning % (durationHigh + durationLow);

    if(timeRunning <= durationHigh) {
      digitalWrite(pin, 1);
    } else {
      digitalWrite(pin, 0);
    }
  }

  // Check if running.
  bool check() {
    if(millis() < timeEnd) {
      return 1;
    } else {
      return 0;
    }
  }
};



led led1Obj(PIN_LED1);
led led2Obj(PIN_LED2);


void           setup() {
  delay(2000);           // DEBUG
  Serial.begin(115200);  // DEBUG
  delay(2000);           // DEBUG
  Serial.println("BEGIN"); // DEBUG
  pinMode(PIN_IR_INPUT, INPUT);
  pinMode(PIN_STATE_OUT, OUTPUT);
  digitalWrite(PIN_STATE_OUT, 0);
  attachInterrupt(PIN_IR_INPUT, irInterrupt, CHANGE);
  /*
  DDRB |= 1 << PIN_STATE_OUT;  // Set 3 as output.
  DDRB &= 0 << PIN_IR_INPUT;   // Set 4 as input.
  DDRB |= 1 << PIN_LED1;  // Set 1 as output.
  DDRB |= 1 << PIN_LED2;  // Set 0 as output.
  
  PORTB |= 1 << DDB3;
  PORTB &= 0 << DDB3;
  (PORTB >> DDB3) & 1;*/
}


void loop() {
  bool           changeState    = 0;  // Whether to change state this loop.
  uint8_t        recievedToggle = 0, recievedAddress = 0, recievedCommand = 0;
  static uint8_t recievedTogglePrev = -1, recievedAddressPrev = -1, recievedCommandPrev = -1;

  // Check for ir.
  if(irCheck(&recievedToggle, &recievedAddress, &recievedCommand)) {
    //Serial.printf("tgl: %u\naddr: 0x%x\tcmd: 0x%x\n", recievedToggle, recievedAddress, recievedCommand);  // DEBUG
    /** TODO: do something with these */
    // Detect only change.
    if(recievedToggle != recievedTogglePrev && recievedAddress != recievedAddressPrev &&
       recievedCommand != recievedCommandPrev) {
         recievedTogglePrev  = recievedToggle;
         recievedAddressPrev = recievedAddress;
         recievedCommandPrev = recievedCommand;
         changeState         = 1;
        }
      } else {
        //Serial.println("ReadErr");  // DEBUG
      }
      
      static uint8_t state = 0, statePrev = -1;
  #define STATE_WAITING 0
  #define STATE_RUNNING 1
  #define STATE_STOPPED 2
      switch(state) {
        case STATE_WAITING:
        if(changeState == 1) {
          // On enter.
          if(state != statePrev) {
            statePrev = state;
          }
        }
        break;
        
        case STATE_RUNNING:
        if(changeState == 1) {
        }
        break;
        
        case STATE_STOPPED:
        if(changeState == 1) {
      }
      break;

    default:
      state = STATE_STOPPED;
      break;
  }

  Serial.print("ALIVE: ");
  Serial.println(millis());
  delay(50);
}
#elif 0

  #include <Arduino.h>



/**
   * pin  | gpio  | meta    | other   | i2c   | remote
   * 1    | 5     | reset   | adc0    |       | reset
   * 2    | 3     | -       | adc3    |       | dataOut
   * 3    | 4     | -       | adc2    |       | dataIn
   * 4    | gnd   | gnd     | -       |       | gnd
   * 5    | 0     | mosi    | pwm0    | sda   | led2 (yellow)
   * 6    | 1     | miso    | pwm1    |       | led1 (blue)
   * 7    | 2     | sck     | adc1    | scl   | 
   * 8    | vcc   | vcc     | -       |       | vcc
   */

  #define PIN_STATE_OUT 3
  #define PIN_IR_INPUT  4
  #define PIN_LED1      1  // MISO
  #define PIN_LED2      0  // MOSI, Serial Tx

void setup() {
  //Serial.begin(9600); // MOSI is Tx
  pinMode(PIN_LED1, OUTPUT);
}

void loop() {
  //Serial.println("Hewwo wowd :3");
  digitalWrite(PIN_LED1, 1);
  delay(500);
  digitalWrite(PIN_LED1, 0);
  delay(500);
}
#elif 1

  #include <Arduino.h>
  #define PIN_STATE_OUT 3
  #define PIN_IR_INPUT  4
  #define PIN_LED1      1
  #define PIN_LED2      0

void setup() {
  pinMode(PIN_IR_INPUT, INPUT);
  pinMode(PIN_STATE_OUT, OUTPUT);
  pinMode(PIN_LED2, OUTPUT);
  pinMode(PIN_LED1, OUTPUT);
  digitalWrite(PIN_STATE_OUT, 0);
  digitalWrite(PIN_LED1, 0);
}

void loop() {
  digitalWrite(PIN_LED2, digitalRead(PIN_IR_INPUT));
  digitalWrite(PIN_LED1, 1);
  digitalWrite(PIN_LED2, digitalRead(PIN_IR_INPUT));
  digitalWrite(PIN_LED1, 0);

}


#endif

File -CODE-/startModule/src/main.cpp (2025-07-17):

/**
 * PINS
 * pin  | gpio  | meta    | other   | i2c   | remote
 * 1    | 5     | reset   | adc0    |       | reset (also known as reset)
 * 2    | 3     | -       | adc3    |       | dataOut
 * 3    | 4     | -       | adc2    |       | dataIn
 * 4    | gnd   | gnd     | -       |       | gnd
 * 5    | 0     | mosi    | pwm0    | sda   | led2 (yellow)
 * 6    | 1     | miso    | pwm1    |       | led1 (blue)
 * 7    | 2     | sck     | adc1    | scl   | 
 * 8    | vcc   | vcc     | -       |       | vcc
 */
/**
 * RC5 DATA
 * 11<toggle_bit:1><command_type:5><id:5><data:1>
 *  - toggle_bit - helps differentiate between an intended and unintended signal interruption
 *  - command_type - either 7 or 11
 *    - 7 - robot state
 *    - 11 - set id
 *  - id - the id to either verify or set, same as the dip switches on the remote
 *  - data - an additional bit that does stuff in pair with the command_type
 *    - command_type == 7 && data == 1 - start
 *    - command_type == 7 && data == 0 - stop
 *    - command_type == 11 - always 0
 */
/**
 * MODULE OUTPUT
 *  - 0 - stop
 *  - 1 - go
 */

/** TODO: Add the led stuff */

#include <Arduino.h>
#include "decoding.h"
#include "parsing.h"

#define PIN_STATE_OUT 3
#define PIN_IR_INPUT  4
#define PIN_LED1      1
#define PIN_LED2      0



enum State { IDLE, READING, DECODING, PARSING, SETTING_OUTPUT };
enum CommandType { ROBOT_STATE = 7, SET_ID = 11 };


#define TX PIN_LED2

#define SHORT_GAP_MAX 1400
#define READ_TIMEOUT  25000

#define LED1_BLINK_TIME 1000
#define LED2_BLINK_TIME 200



void ioInnit() {
  pinMode(PIN_IR_INPUT, INPUT);
  pinMode(PIN_STATE_OUT, OUTPUT);
  pinMode(PIN_LED2, OUTPUT);
  pinMode(PIN_LED1, OUTPUT);
  digitalWrite(PIN_IR_INPUT, 0);
  digitalWrite(PIN_STATE_OUT, 0);
  digitalWrite(PIN_LED1, 0);
  digitalWrite(PIN_LED2, 0);
}


void setup() {
  ioInnit();
}

void loop() {
  static State    state      = State::IDLE;
  static uint32_t trigMicros = 0, trigMicrosPrev = 0;
  uint32_t        microsNow = 0;
  static uint32_t buffer;
  bool            irVal     = 0;
  static bool     irValPrev = 0;

  static uint16_t decodedBits = 0;
  static parsed   parsedObj;

  static uint8_t id     = 0;
  static bool    output = 0, outputPrev = 0;
  static bool    outputL1 = 0, outputL1Prev = 0;
  static bool    outputL2 = 0, outputL2Prev = 0;

  static uint8_t led2BlinkCount = 0;
  static uint32_t led2BlinkPrev = 0;
  static uint32_t led1BlinkPrev = 0;

  uint32_t millisNow = 0;


  switch(state) {
    case State::IDLE:
      microsNow = micros();
      irVal     = !digitalRead(PIN_IR_INPUT);
      if(irVal == 1) {
        trigMicros = microsNow;
        state      = State::READING;
      }
      break;

    case State::READING:
      microsNow = micros();
      irVal     = !digitalRead(PIN_IR_INPUT);
      if(irVal != irValPrev) {
        irValPrev      = irVal;
        trigMicrosPrev = trigMicros;
        trigMicros     = microsNow;
        if(trigMicros - trigMicrosPrev > SHORT_GAP_MAX) {
          buffer = buffer << 1;
          buffer = buffer + 1;
        } else {
          buffer = buffer << 1;
        }
      } else if(microsNow - trigMicros > READ_TIMEOUT) {
        state = State::DECODING;
      }
      break;

    case State::DECODING:
      decodedBits = decodeTheMess(buffer);
      state       = State::PARSING;
      break;

    case State::PARSING:
      parsedObj = parse(decodedBits);
      state     = State::SETTING_OUTPUT;
      break;

    case State::SETTING_OUTPUT:
      switch(parsedObj.command_type) {
        case CommandType::ROBOT_STATE:
          if(parsedObj.id == id) {
            output = parsedObj.data;
          }
          break;

        case CommandType::SET_ID:
          id = parsedObj.id;
          outputL2 = 0;
          led2BlinkCount = 4;
          break;

        default:
          break;
      }
      buffer = 0;
      state  = State::IDLE;
      break;

    default:
      break;
  }

  millisNow = millis();

  if(led2BlinkCount > 0) {
    if(millisNow - led2BlinkPrev > LED2_BLINK_TIME) {
      led2BlinkPrev = millisNow;
      outputL2 = !outputL2;
      led2BlinkCount--;
    }
  }
  if(millisNow - led1BlinkPrev > LED1_BLINK_TIME) {
    led1BlinkPrev = millisNow;
    outputL1 = !outputL1;
  }


  if(output != outputPrev) {
    outputPrev = output;
    digitalWrite(PIN_STATE_OUT, output);
    outputL2 = output;
  }
  if(outputL1 != outputL1Prev) {
    outputL1Prev = outputL1;
    digitalWrite(PIN_LED1, outputL1);
  }
  if(outputL2 != outputL2Prev) {
    outputL2Prev = outputL2;
    digitalWrite(PIN_LED2, outputL2);
  }
}

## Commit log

2024-08-31 Copied from old repo
    [Components_referee_remote_control_V0_01.ods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]
2024-09-05 Updated remote BOM
    Updated sumec remote idk what i updated but its different
    [Remote_BOM.xlsx]
2024-10-14 Schematic update
    Font update
    [Remote.kicad_sch]
2024-10-15 some 3 updates
    [Remote.kicad_pcb]
2025-04-14 bom change
    [Remote_BOM.xlsx]
